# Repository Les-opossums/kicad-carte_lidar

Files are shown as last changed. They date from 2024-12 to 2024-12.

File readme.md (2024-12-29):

# Carte lidar - opossum 2025
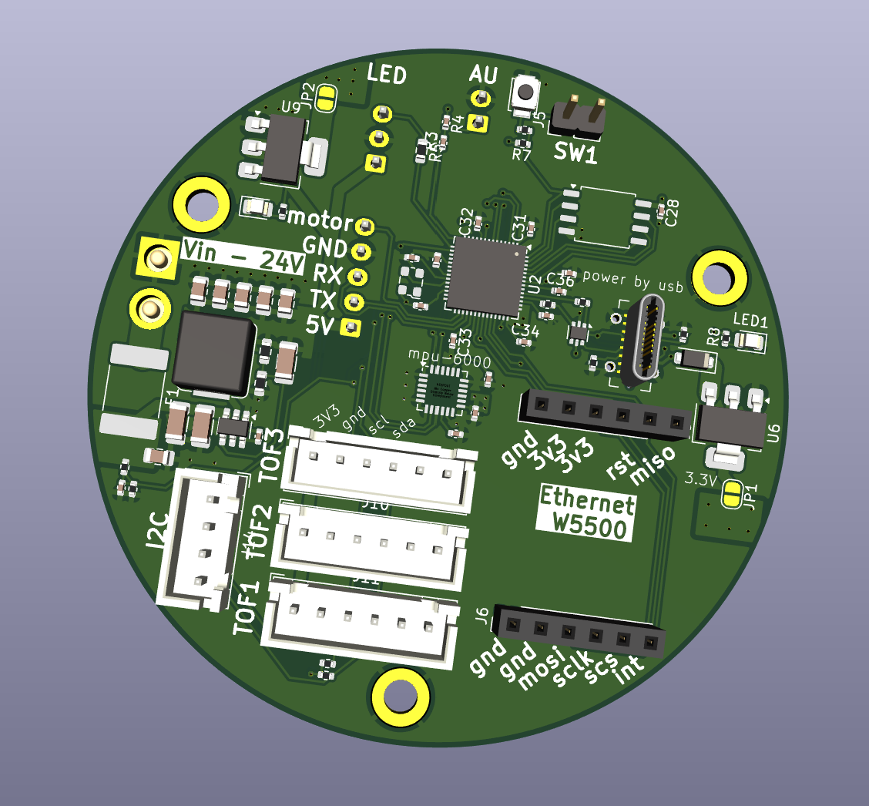
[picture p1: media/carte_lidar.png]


Cette carte se trouve dans le mat de balise du robot opossum.
Elle doit : 
- Gérer le lidar A2M12 (alimentation + récupération des données).
- Gérer un accéléromètre mpu-6000 et l'utiliser pour corriger les points lidar.
- Gérer le ruban led qui entoure le mat de balise
La communication avec le raspberry pi se fait soit par USB (également utilisé pour programmer le rp2040) soit via ethernet avec un module W5500.

On peut également y brancher 3 TOFs de type vl53l0x et une carte d'extension i2c pour en brancher plus. 

L'alimentation du rp2040 se fait au choix soit par la tension d'entrée 24v également utilisée par le lidar, soit par l'usb.

## Intégration mécanique dans le robot 
Voici un appercu de la carte dans le mat de balise du robot :
 
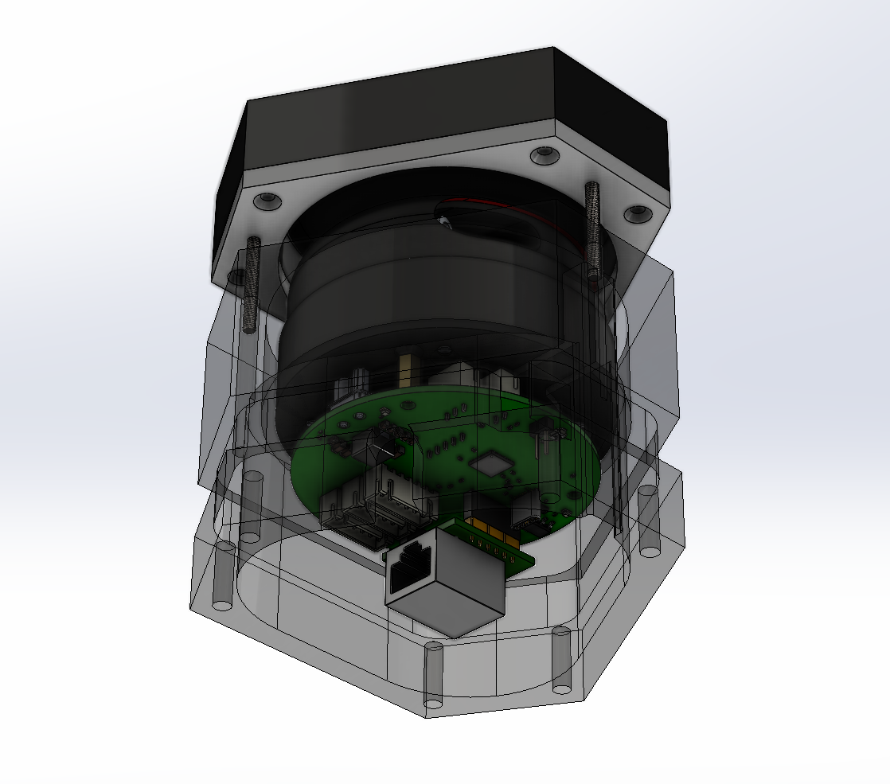
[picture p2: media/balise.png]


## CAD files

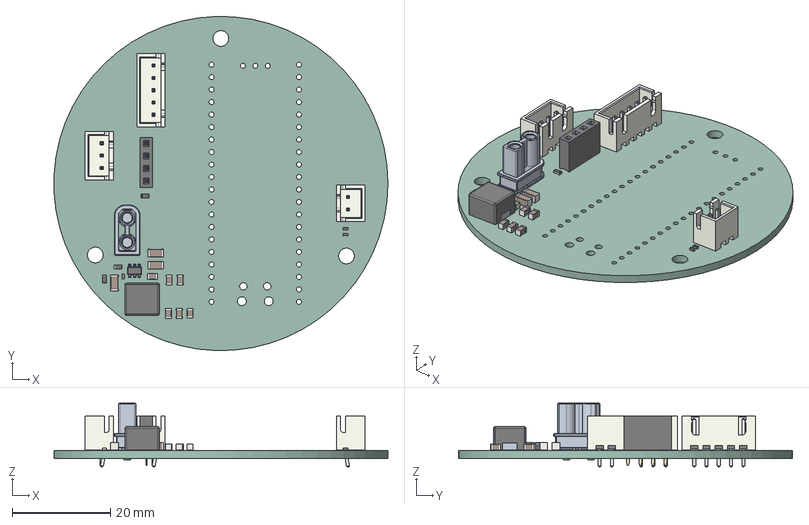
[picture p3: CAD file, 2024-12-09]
carte_lidar.step
68.0 x 68.0 x 13.0 mm
SOT_23_6
C_0805_2012Metric x 6
JST_B5B_XH_A
C_0402_1005Metric x 3
C_1206_3216Metric x 3
JST_B2B_XH_A
ASSEMBLY
PinSocket_1x04_P254mm_Vertical
R_0603_1608Metric x 3
JST_B3B_XH_A
CQ assembly
carte_lidar_PCB

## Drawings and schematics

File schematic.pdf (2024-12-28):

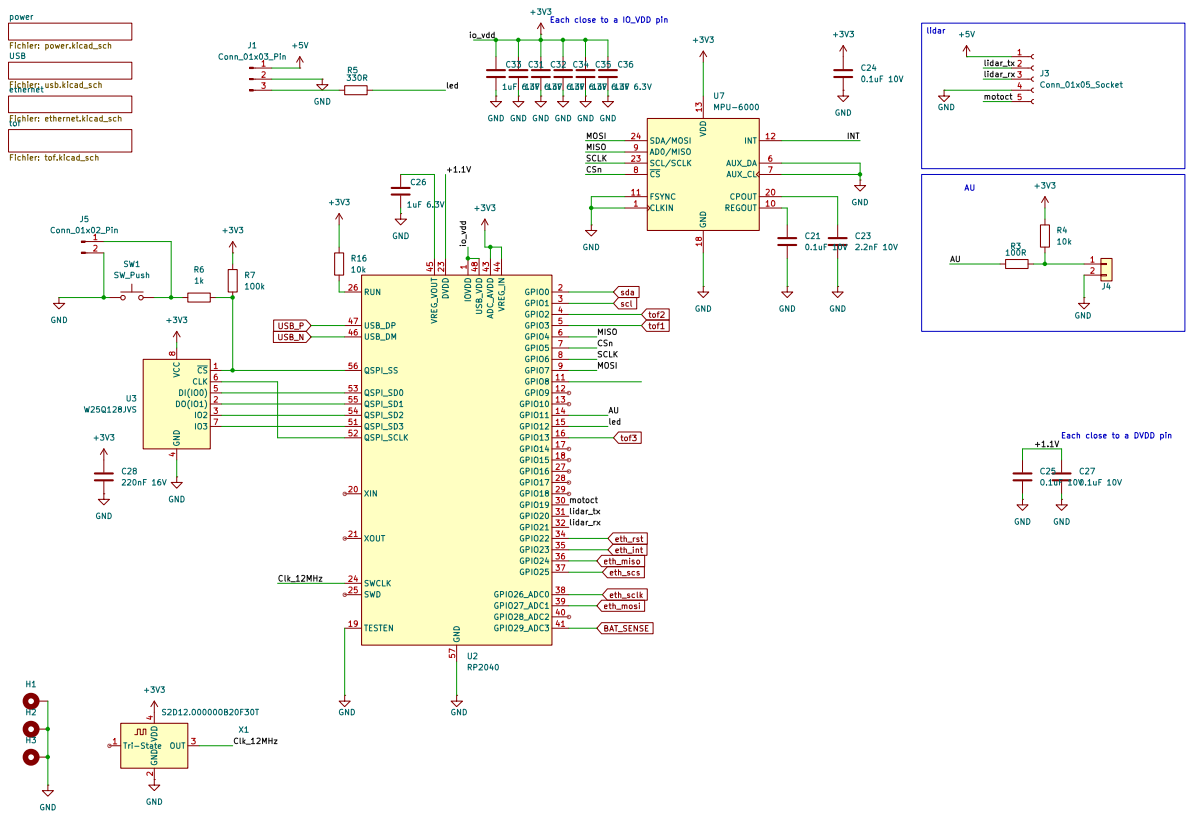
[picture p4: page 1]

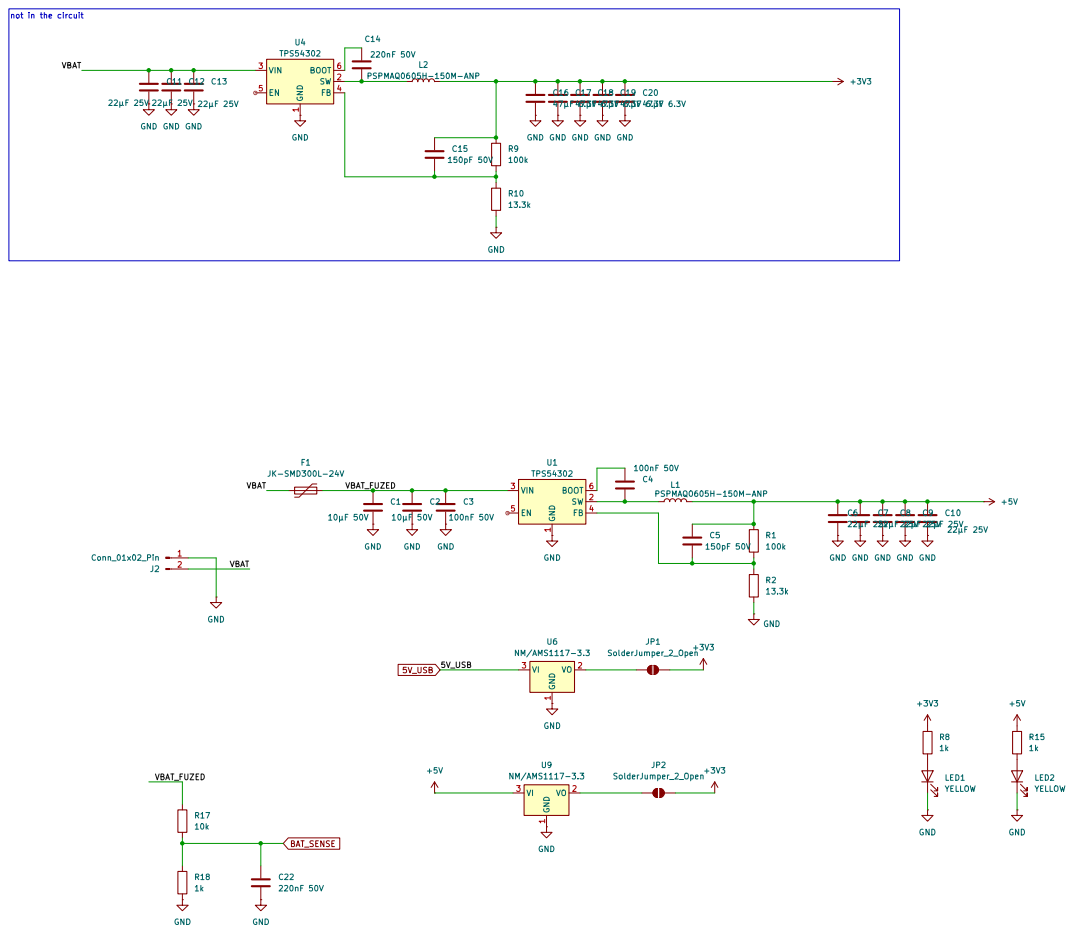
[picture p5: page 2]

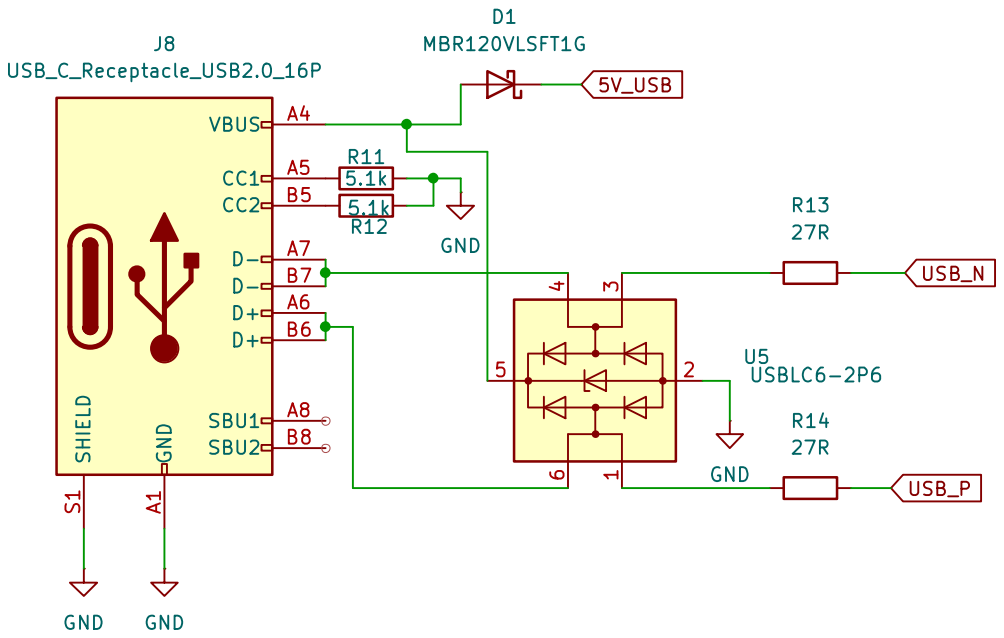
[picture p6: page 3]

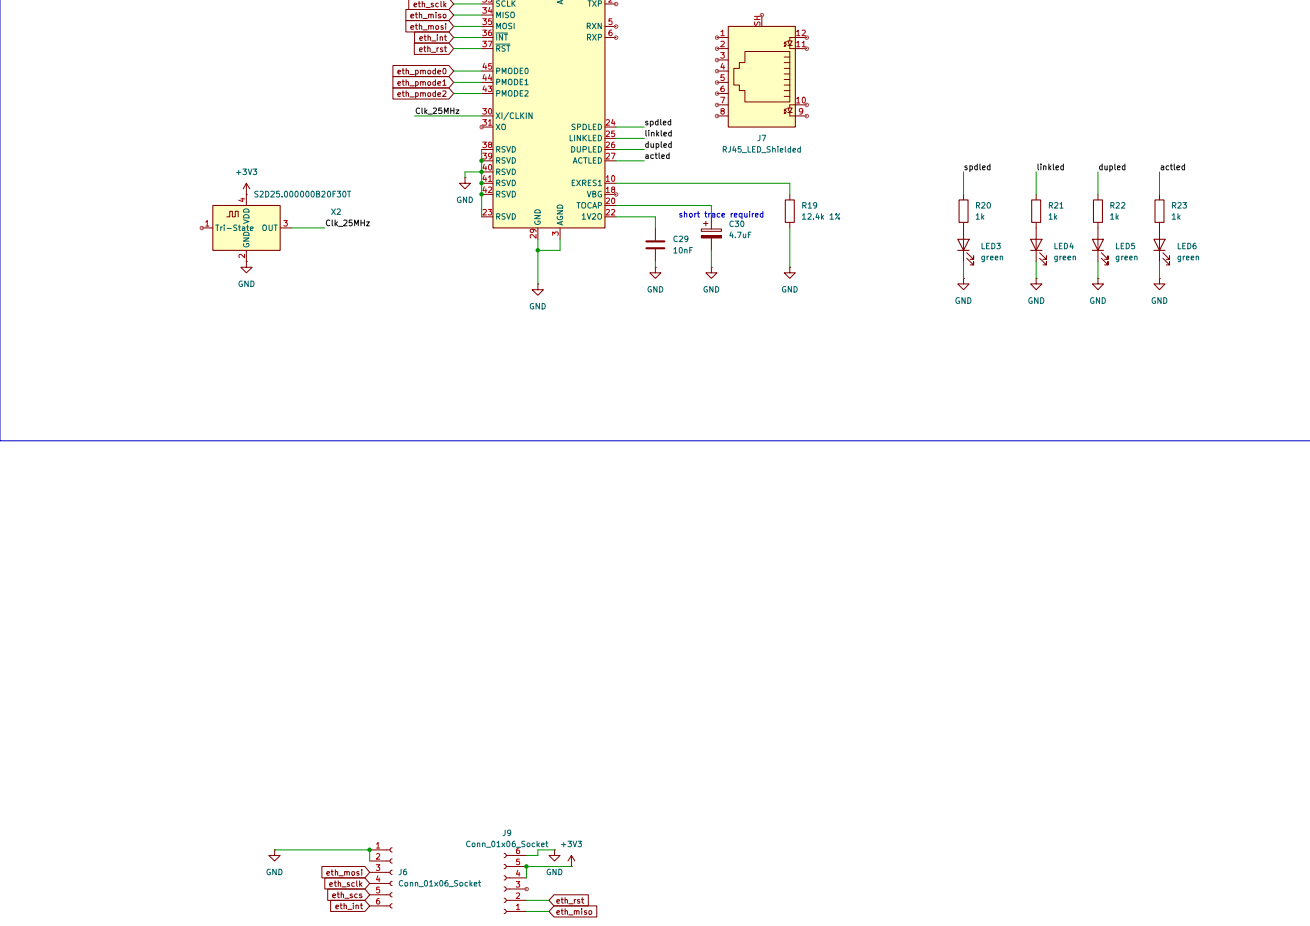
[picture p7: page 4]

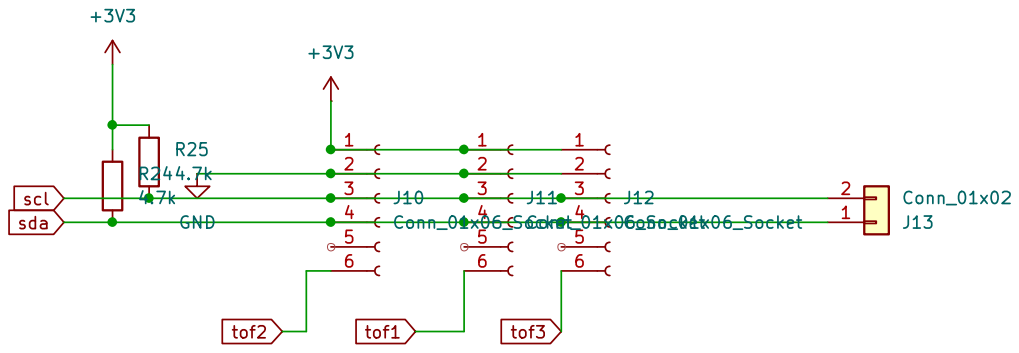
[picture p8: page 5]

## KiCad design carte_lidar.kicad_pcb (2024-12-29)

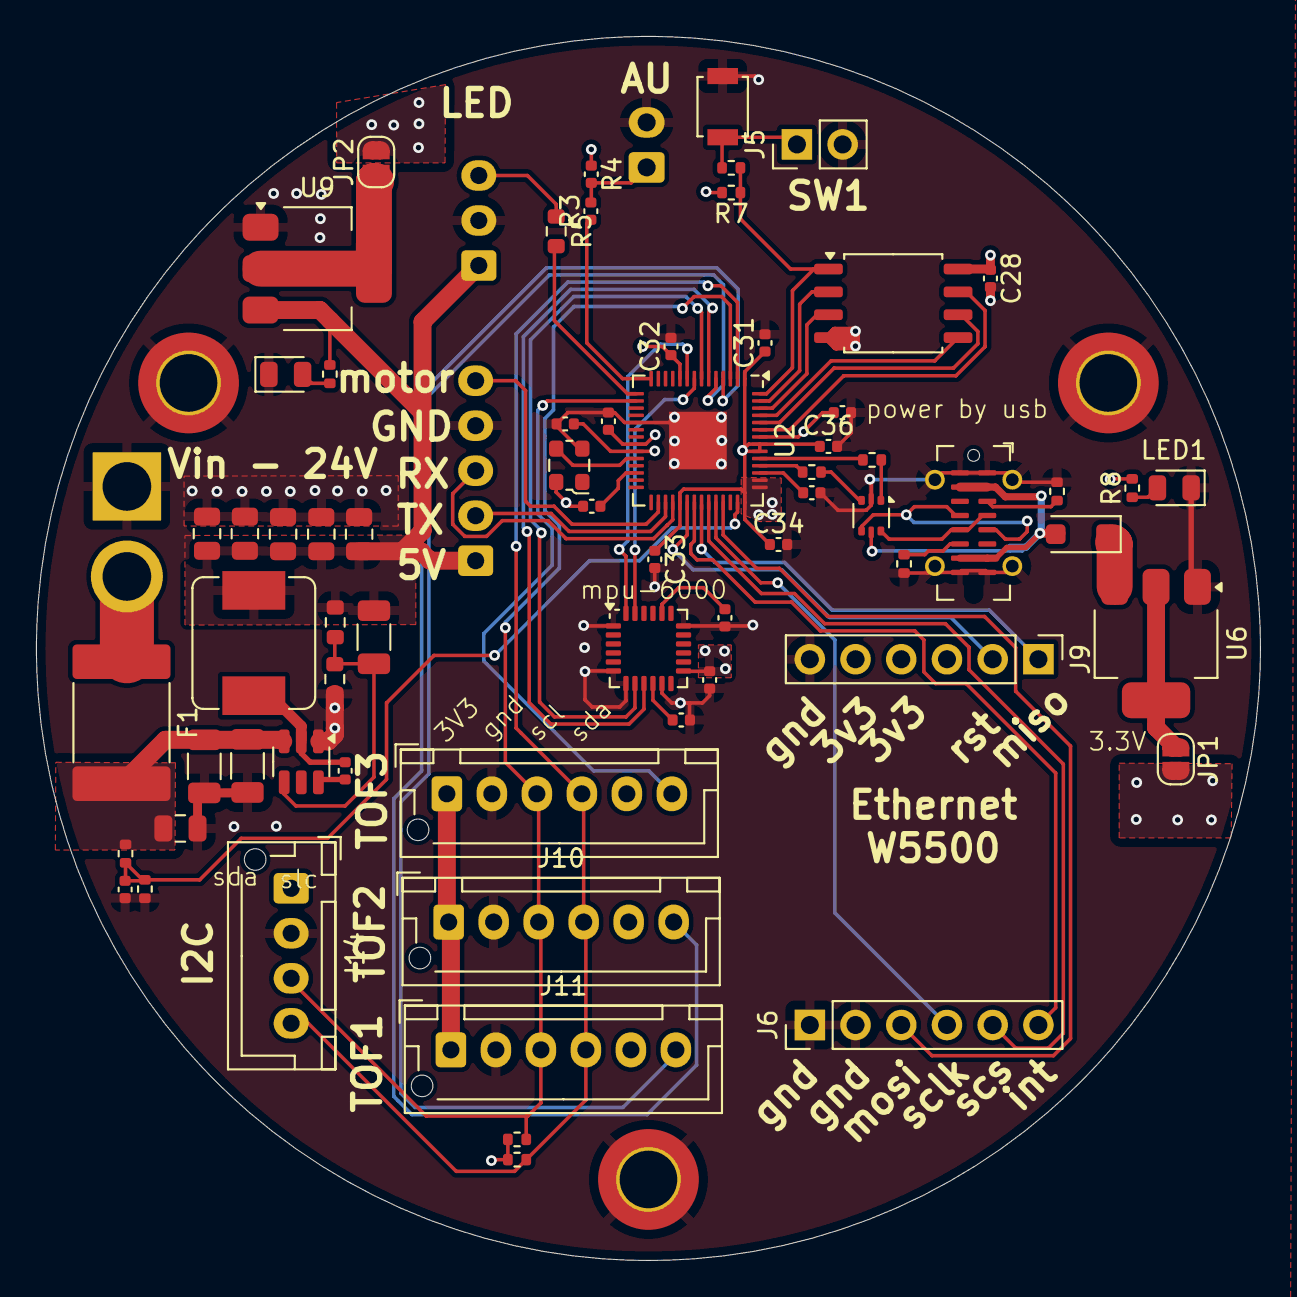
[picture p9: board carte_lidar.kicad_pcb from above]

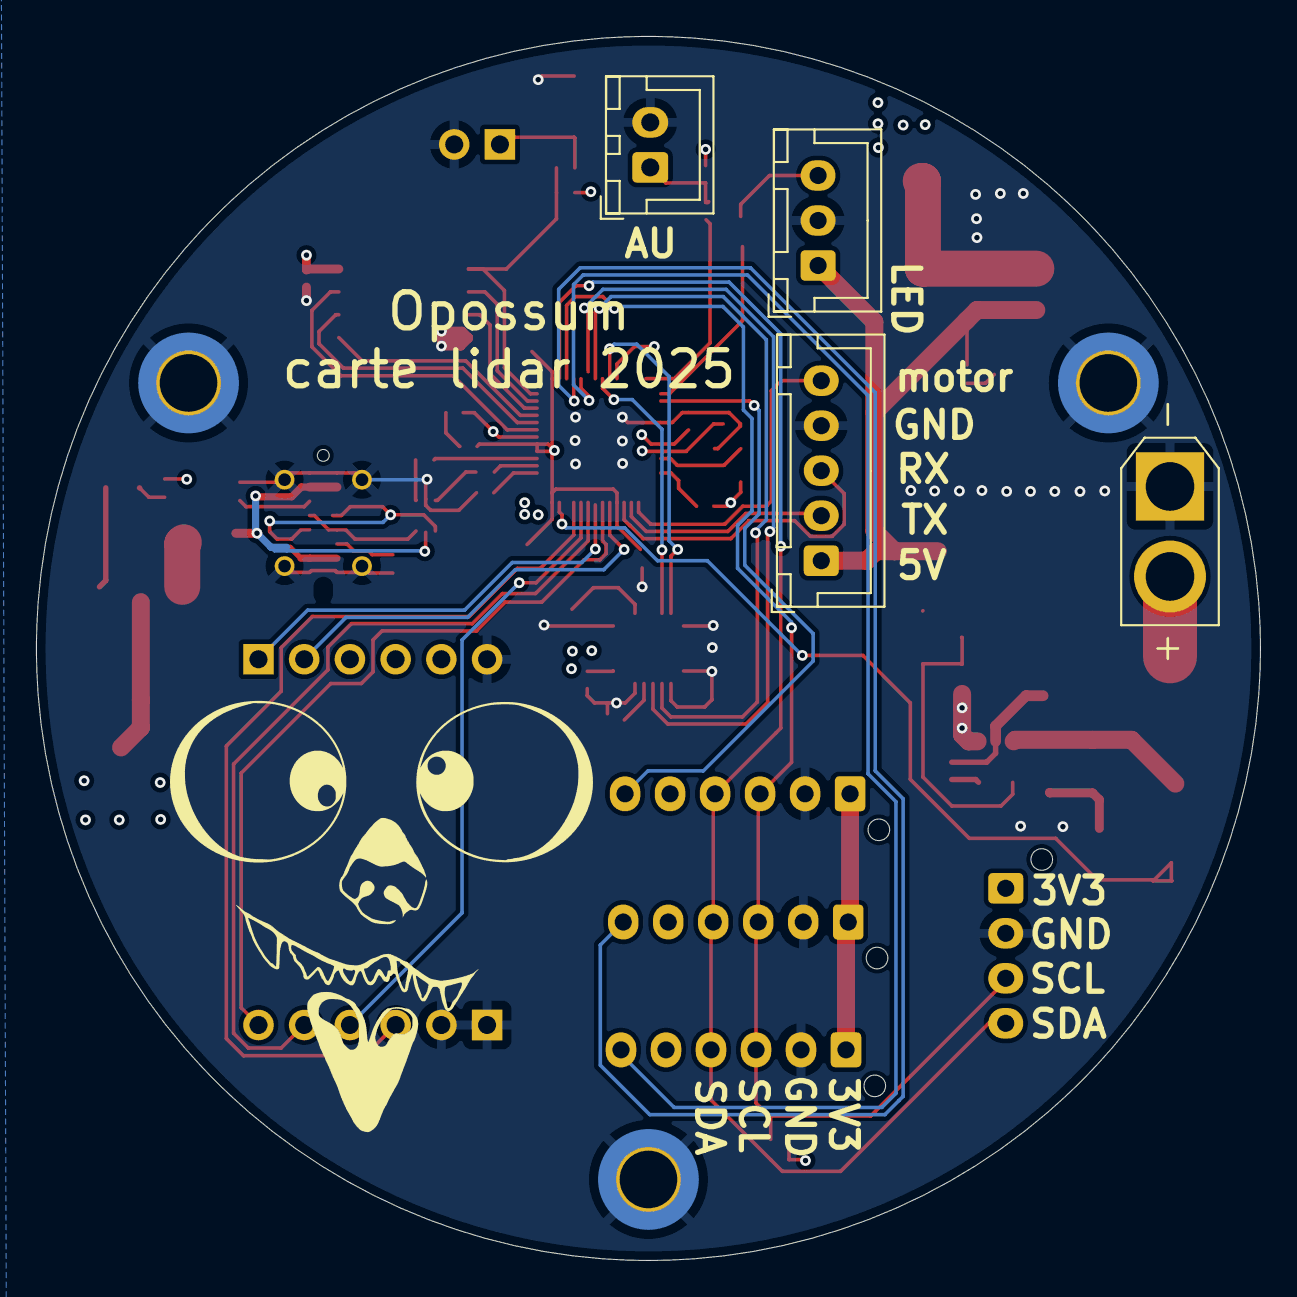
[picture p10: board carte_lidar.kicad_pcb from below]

Board: 4 copper layers, 68.0 x 68.0 mm, 73 parts (4 on the bottom side), 58 nets.

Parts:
C1, C2: 10µF 50V; C_1206_3216Metric
C3: 100nF 50V; C_0805_2012Metric
C4: 100nF 50V; C_0402_1005Metric
C5: 150pF 50V; C_1206_3216Metric
C6, C7, C8, C9, C10: 22µF 25V; C_0805_2012Metric
C21, C24, C25, C27: 0.1uF 10V; C_0402_1005Metric
C22: 220nF 50V; C_0402_1005Metric
C23: 2.2nF 10V; C_0402_1005Metric
C26, C31, C32, C33, C34, C35, C36: 1uF 6.3V; C_0402_1005Metric
C28: 220nF 16V; C_0402_1005Metric
D1: MBR120VLSFT1G; D_SOD-123F
F1: JK-SMD300L-24V; Fuse_2920_7451Metric
H1, H2, H3: MountingHole_Pad; MountingHole_3.2mm_M3_DIN965_Pad_TopBottom
J1: Conn_01x03_Pin; JST_XH_B3B-XH-A_1x03_P2.50mm_Vertical
J2: Conn_01x02_Pin; AMASS_XT30U-F_1x02_P5.0mm_Vertical
J3: Conn_01x05_Socket; JST_XH_B5B-XH-A_1x05_P2.50mm_Vertical
J4: Conn_01x02; JST_XH_B2B-XH-A_1x02_P2.50mm_Vertical
J5: Conn_01x02_Pin; PinHeader_1x02_P2.54mm_Vertical
J6, J9: Conn_01x06_Socket; PinHeader_1x06_P2.54mm_Vertical
J8: USB_C_Receptacle_USB2.0_16P; USB_C_Receptacle_G-Switch_GT-USB-7051x
J10, J11, J12: Conn_01x06_Socket; JST_XH_B6B-XH-AM_1x06_P2.50mm_Vertical
J14: Conn_01x04_Socket; JST_XH_B4B-XH-AM_1x04_P2.50mm_Vertical
JP1, JP2: SolderJumper_2_Open; SolderJumper-2_P1.3mm_Open_RoundedPad1.0x1.5mm
L1: PSPMAQ0605H-150M-ANP; Prod_Tech_7.1x6.6mm
LED1, LED2: YELLOW; LED_0805_2012Metric
R1: 100k; R_0603_1608Metric
R2: 13.3k; R_0603_1608Metric
R3: 100R; C_0402_1005Metric
R4, R16: 10k; C_0402_1005Metric
R5: 330R; R_0603_1608Metric
R6, R8, R15, R18: 1k; R_0402_1005Metric
R7: 100k; R_0402_1005Metric
R11, R12: 5.1k; R_0402_1005Metric
R13, R14: 27R; R_0402_1005Metric
R17: 10k; R_0402_1005Metric
R24, R25: 4.7k; R_0402_1005Metric
SW1: SW_Push; SW_SPST_B3U-1000P
U1: TPS54302; SOT-23-6
U2: RP2040; QFN-56-1EP_7x7mm_P0.4mm_EP3.2x3.2mm
U3: W25Q128JVS; SOIC-8_5.23x5.23mm_P1.27mm
U5: USBLC6-2P6; SOT-666
U6, U9: NM/AMS1117-3.3; SOT-223-3_TabPin2
U7: MPU-6000; InvenSense_QFN-24_4x4mm_P0.5mm
X1: S2D12.000000B20F30T; Oscillator_SMD_ECS_2520MV-xxx-xx-4Pin_2.5x2.0mm

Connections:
5V_USB: D1.1 (K), U6.3 (VI)
+3V3: C24.1, C28.1, C31.1, C32.1, C33.1, C34.1, C35.1, C36.1, J9.4, J9.5, J10.1, J11.1, J12.1, J14.1, JP1.2 (B), JP2.2 (B), R4.1, R7.2, R8.2, R16.1, R24.2, R25.2, U2.1 (IOVDD), U2.10 (IOVDD), U2.22 (IOVDD), U2.33 (IOVDD), U2.42 (IOVDD), U2.43 (ADC_AVDD), U2.44 (VREG_IN), U2.48 (USB_VDD), U2.49 (IOVDD), U3.8 (VCC), U7.13 (VDD), X1.4 (VDD)
+5V: C5.1, C6.1, C7.1, C8.1, C9.1, C10.1, J1.1, J3.1, L1.2, R1.1, R15.2, U9.3 (VI)
/+1.1V: C25.1, C27.1, U2.23 (DVDD), U2.50 (DVDD)
/AU: R3.1, U2.14 (GPIO11)
/CSn: U2.7 (GPIO5), U7.8 (~CS)
/Clk_12MHz: U2.24 (SWCLK), X1.3 (OUT)
/MISO: U2.6 (GPIO4), U7.9 (AD0/MISO)
/MOSI: U2.9 (GPIO7), U7.24 (SDA/MOSI)
/SCLK: U2.8 (GPIO6), U7.23 (SCL/SCLK)
/led: R5.2, U2.15 (GPIO12)
/lidar_rx: J3.3, U2.32 (GPIO21)
/lidar_tx: J3.2, U2.31 (GPIO20)
/motoct: J3.5, U2.30 (GPIO19)
/power/VBAT: F1.1, J2.2
/power/VBAT_FUZED: C1.1, C2.1, C3.1, F1.2, R17.2, U1.3 (VIN)
BAT_SENSE: C22.1, R17.1, R18.2, U2.41 (GPIO29_ADC3)
GND: C1.2, C2.2, C3.2, C6.2, C7.2, C8.2, C9.2, C10.2, C21.2, C22.2, C23.2, C24.2, C25.2, C26.2, C27.2, C28.2, C31.2, C32.2, C33.2, C34.2, C35.2, C36.2, H1.1, H2.1, H3.1, J1.2, J2.1, J3.4, J4.2, J5.2, J6.1, J6.2, J8.A1 (GND), J8.A12 (GND), J8.B1 (GND), J8.B12 (GND), J8.S1 (SHIELD), J9.6, J10.2, J11.2, J12.2, J14.2, LED1.1 (K), LED2.1 (K), R2.2, R11.2, R12.2, R18.1, SW1.1, U1.1 (GND), U2.19 (TESTEN), U2.57 (GND), U3.4 (GND), U5.2 (GND), U6.1 (GND), U7.1 (CLKIN), U7.6 (AUX_DA), U7.7 (AUX_CL), U7.11 (FSYNC), U7.18 (GND), U9.1 (GND), X1.2 (GND)
unnamed: D1.2 (A), J8.A4 (VBUS), J8.A9 (VBUS), J8.B4 (VBUS), J8.B9 (VBUS), U5.5 (VBUS)
unnamed: J1.3, R5.1
unnamed: J4.1, R3.2, R4.2
unnamed: J5.1, R6.2, SW1.2
unnamed: J8.A5 (CC1), R11.1
unnamed: J8.B5 (CC2), R12.1
unnamed: J8.A6 (D+), J8.B6 (D+), U5.6 (I/O1)
unnamed: J8.A7 (D-), J8.B7 (D-), U5.4 (I/O2)
unnamed: JP1.1 (A), U6.2 (VO)
unnamed: JP2.1 (A), U9.2 (VO)
unnamed: LED1.2 (A), R8.1
unnamed: LED2.2 (A), R15.1
unnamed: R13.1, U5.3 (I/O2)
unnamed: R14.1, U5.1 (I/O1)
unnamed: C4.1, U1.6 (BOOT)
unnamed: C5.2, R1.2, R2.1, U1.4 (FB)
unnamed: C4.2, L1.1, U1.2 (SW)
unnamed: U2.52 (QSPI_SCLK), U3.6 (CLK)
unnamed: U2.53 (QSPI_SD0), U3.5 (DI(IO0))
unnamed: U2.55 (QSPI_SD1), U3.2 (DO(IO1))
unnamed: U2.54 (QSPI_SD2), U3.3 (IO2)
unnamed: U2.51 (QSPI_SD3), U3.7 (IO3)
unnamed: R6.1, R7.1, U2.56 (QSPI_SS), U3.1 (~CS)
unnamed: R16.2, U2.26 (RUN)
unnamed: C26.1, U2.45 (VREG_VOUT)
unnamed: C23.1, U7.20 (CPOUT)
unnamed: C21.1, U7.10 (REGOUT)
USB_N: R13.2, U2.46 (USB_DM)
USB_P: R14.2, U2.47 (USB_DP)
eth_int: J6.6, U2.35 (GPIO23)
eth_miso: J9.1, U2.36 (GPIO24)
eth_mosi: J6.3, U2.39 (GPIO27_ADC1)
eth_rst: J9.2, U2.34 (GPIO22)
eth_sclk: J6.4, U2.38 (GPIO26_ADC0)
eth_scs: J6.5, U2.37 (GPIO25)
scl: J10.3, J11.3, J12.3, J14.3, R25.1, U2.3 (GPIO1)
sda: J10.4, J11.4, J12.4, J14.4, R24.1, U2.2 (GPIO0)
tof1: J11.6, U2.5 (GPIO3)
tof2: J10.6, U2.4 (GPIO2)
tof3: J12.6, U2.16 (GPIO13)

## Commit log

2024-12-08 first commit only for cao
    [carte_lidar.kicad_pcb, carte_lidar.kicad_sch, carte_lidar.step]
2024-12-24 update all
    [accelerometer.kicad_sch, carte_lidar.kicad_pcb, carte_lidar.kicad_sch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]
2024-12-26 add ethernet in schematic
    [carte_lidar.kicad_pcb, carte_lidar.kicad_sch, ethernet.kicad_sch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]
2024-12-29 update silkscreen layer
    [carte_lidar.kicad_pcb, tof.kicad_sch]
